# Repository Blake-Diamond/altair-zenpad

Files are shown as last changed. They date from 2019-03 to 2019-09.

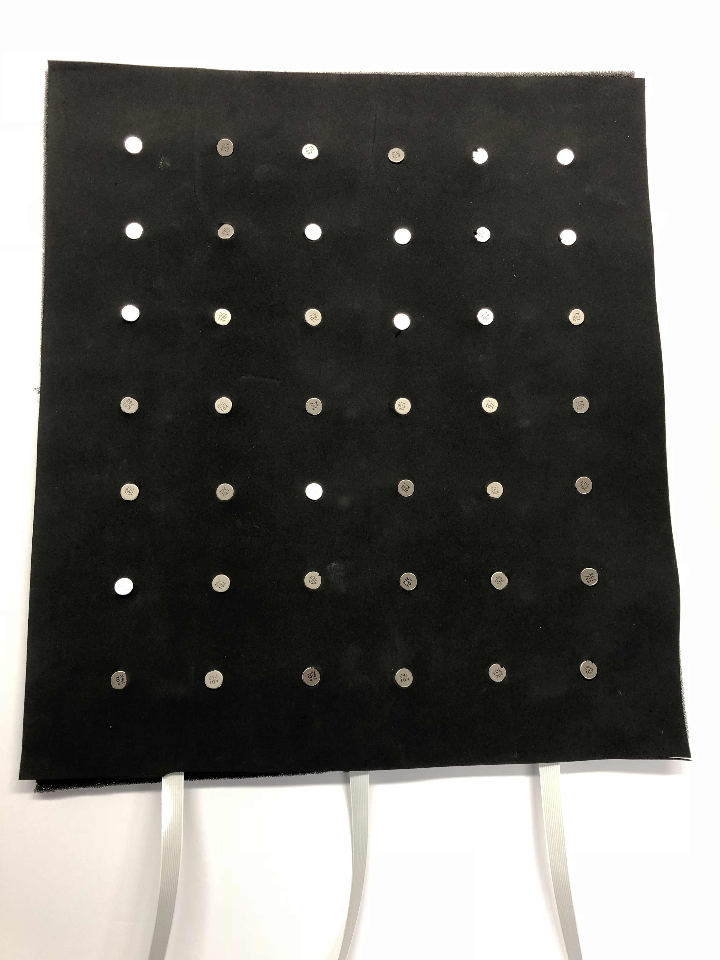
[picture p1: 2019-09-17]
Media/PHOTOS/image_67164417.JPG

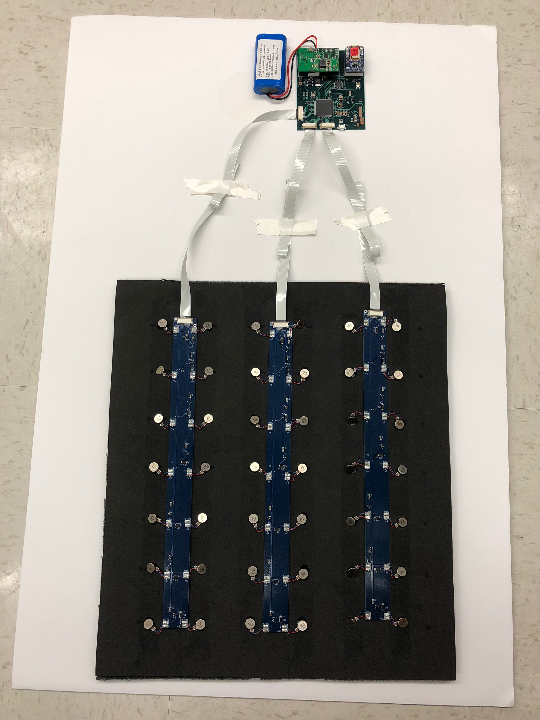
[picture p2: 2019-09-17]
Media/PHOTOS/IMG-0710.JPG

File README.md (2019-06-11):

# UC Santa Barbara - ECE Department 
## EE Capstone 2018-2019

### Contributors: Evan Blasband, Blake Diamond, Adam Gulliver, Zack Klebanoff

https://capstone.engineering.ucsb.edu/projects/altair-zenpad

This repository contains all of our arduino and android studio code for Altair Zenpad, a smart massage pad that you can control from your fingertips. There are 3 imporant aspect of this respository that contiain all of the necessary reference documents for future development and use of the ZenPad, described below:

## Hardware

PCB/Altair Massage Pad: contains all PCB projects (EAGLE) for Main and Peripheral PCB.

## Firmware

Winter_Demo: This folder contains all of the firmware that is need to flash the Teensy 3.6 using the Arduino IDE. This includes all associated header files that support use of the Bluetooth and PMIC. Some small changes are needed in order to program a Teensy board with the Arduino IDE, which can be found here: https://www.pjrc.com/teensy/tutorial.html

## Software

Zenpad-App/ZenPad: This folder contains the software project for the ZenPad app, which can be accessed by downloading and opening with Android Studio. Someone with Android SW development experience is needed in order to properly open and run the app, which was developed on a Nexus 5 phone.

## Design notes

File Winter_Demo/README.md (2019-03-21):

Code for Winter Demo

Combines operating the motors via simple bluetooth communication and incorporates simple reading of the PMIC registers.

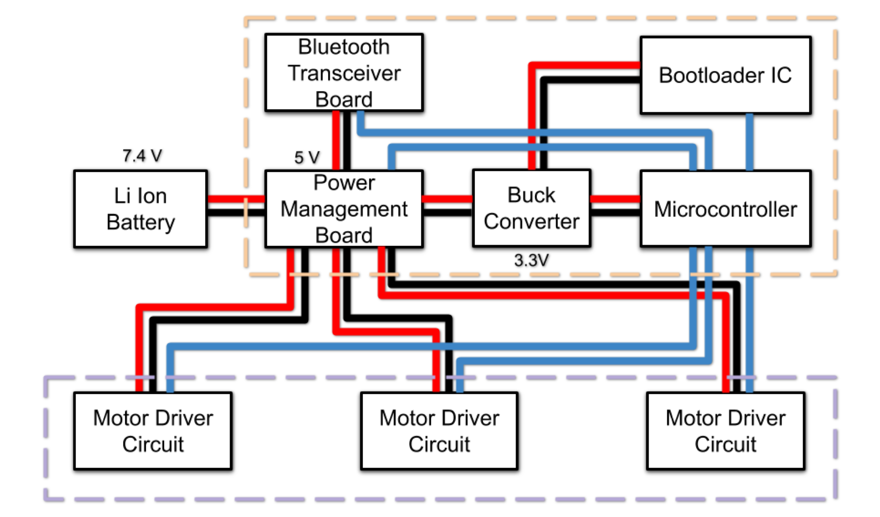
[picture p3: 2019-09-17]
Media/PHOTOS/Submitted images/blockDiagram.png

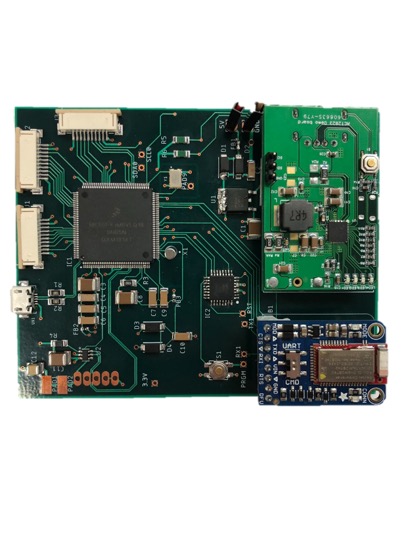
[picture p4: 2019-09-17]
Media/PHOTOS/Picture1.jpg

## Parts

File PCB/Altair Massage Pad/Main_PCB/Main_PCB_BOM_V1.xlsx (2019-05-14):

Part | Value | Device | Package | Description | ALLIED_NUMBER | ALLIED_PRICE-STOCK | DESCRIPTION | DIGI-KEY_PART_NUMBER | DIGI-KEY_PURCHASE_URL | HEIGHT | MANUFACTURER_NAME | MANUFACTURER_PART_NUMBER | MF | MOUSER_PART_NUMBER | MOUSER_PRICE-STOCK | MP | MPN | OC_FARNELL | OC_NEWARK | PACKAGE | RS_PART_NUMBER | RS_PRICE-STOCK | SPICEPREFIX | TP_SIGNAL_NAME | VENDOR
B1 |  | FE08-1 | FE08-1 | Headers & Wire Housings PCB RECPT 8P W/HOOKS TOP ENTRY |  |  |  |  |  |  | Molex | 22-02-2085 |  | 538-22-02-2085 | https://www.mouser.com/ProductDetail/Molex/22-02-2085
C1 | 2.2uF | C-USC1812K | C1812K | CAPACITOR, American symbol |  |  |  |  |  | 2.5mm | KEMET | C1812C225K1RACTU |  | 80-C1812C225K1R | https://www.mouser.com/ProductDetail/KEMET/C1812C225K1RACTU |  |  |  |  |  |  |  | C
C2 | 0.1uF | C-USC1808 | C1808 | CAPACITOR, American symbol |  |  |  |  |  | 0.9mm | KEMET | C1808C104KCRACTU (https://www.mouser.com/ProductDetail/KEMET/C1808C104KCRACTU?qs=sGAEpiMZZMs0AnBnWHyRQOl0HKfxQ2GIqnSeW6m289A%3D) |  | 80-C1808C104KCR | https://www.mouser.com/Passive-Components/Capacitors/Ceramic-Capacitors/MLCCs-Multilayer-Ceramic-Capacitors/Multilayer-Ceramic-Capacitors-MLCC-SMD-SMT/_/N-bkr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 |  |  |  |  |  |  |  | C
C3 | 2.2uF | C-USC1812K | C1812K | CAPACITOR, American symbol |  |  |  |  |  | 2.5mm | KEMET | C1812C225K1RACTU |  | 80-C1812C225K1R | https://www.mouser.com/ProductDetail/KEMET/C1812C225K1RACTU |  |  |  |  |  |  |  | C
C4 | 10nF | C-USC1808 | C1808 | CAPACITOR, American symbol |  |  |  |  |  | 1.4mm | KEMET | C1808C103KCRACTU |  | 80-C1808C103KCR | https://www.mouser.com/ProductDetail/KEMET/C1808C103KCRACTU |  |  |  |  |  |  |  | C
C5 | 10nF | C-USC1808 | C1808 | CAPACITOR, American symbol |  |  |  |  |  | 1.4mm | KEMET | C1808C103KCRACTU |  | 80-C1808C103KCR | https://www.mouser.com/ProductDetail/KEMET/C1808C103KCRACTU |  |  |  |  |  |  |  | C
C6 | 0.1uF | C-USC1808 | C1808 | CAPACITOR, American symbol |  |  |  |  |  | 0.9mm | KEMET | C1808C104KCRACTU (https://www.mouser.com/ProductDetail/KEMET/C1808C104KCRACTU?qs=sGAEpiMZZMs0AnBnWHyRQOl0HKfxQ2GIqnSeW6m289A%3D) |  | 80-C1808C104KCR | https://www.mouser.com/Passive-Components/Capacitors/Ceramic-Capacitors/MLCCs-Multilayer-Ceramic-Capacitors/Multilayer-Ceramic-Capacitors-MLCC-SMD-SMT/_/N-bkr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 |  |  |  |  |  |  |  | C
C7 | 0.1uF | C-USC1808 | C1808 | CAPACITOR, American symbol |  |  |  |  |  | 0.9mm | KEMET | C1808C104KCRACTU (https://www.mouser.com/ProductDetail/KEMET/C1808C104KCRACTU?qs=sGAEpiMZZMs0AnBnWHyRQOl0HKfxQ2GIqnSeW6m289A%3D) |  | 80-C1808C104KCR | https://www.mouser.com/Passive-Components/Capacitors/Ceramic-Capacitors/MLCCs-Multilayer-Ceramic-Capacitors/Multilayer-Ceramic-Capacitors-MLCC-SMD-SMT/_/N-bkr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 |  |  |  |  |  |  |  | C
C8 | 2.2uF | C-USC1812K | C1812K | CAPACITOR, American symbol |  |  |  |  |  | 2.5mm | KEMET | C1812C225K1RACTU |  | 80-C1812C225K1R | https://www.mouser.com/ProductDetail/KEMET/C1812C225K1RACTU |  |  |  |  |  |  |  | C
C9 | 0.1uF | C-USC1808 | C1808 | CAPACITOR, American symbol |  |  |  |  |  | 0.9mm | KEMET | C1808C104KCRACTU (https://www.mouser.com/ProductDetail/KEMET/C1808C104KCRACTU?qs=sGAEpiMZZMs0AnBnWHyRQOl0HKfxQ2GIqnSeW6m289A%3D) |  | 80-C1808C104KCR | https://www.mouser.com/Passive-Components/Capacitors/Ceramic-Capacitors/MLCCs-Multilayer-Ceramic-Capacitors/Multilayer-Ceramic-Capacitors-MLCC-SMD-SMT/_/N-bkr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 |  |  |  |  |  |  |  | C
C10 | 0.1uF | C-USC1808 | C1808 | CAPACITOR, American symbol |  |  |  |  |  | 0.9mm | KEMET | C1808C104KCRACTU (https://www.mouser.com/ProductDetail/KEMET/C1808C104KCRACTU?qs=sGAEpiMZZMs0AnBnWHyRQOl0HKfxQ2GIqnSeW6m289A%3D) |  | 80-C1808C104KCR | https://www.mouser.com/Passive-Components/Capacitors/Ceramic-Capacitors/MLCCs-Multilayer-Ceramic-Capacitors/Multilayer-Ceramic-Capacitors-MLCC-SMD-SMT/_/N-bkr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 |  |  |  |  |  |  |  | C
C11 | 2.2uF | C-USC1812K | C1812K | CAPACITOR, American symbol |  |  |  |  |  | 2.5mm | KEMET | C1812C225K1RACTU |  | 80-C1812C225K1R | https://www.mouser.com/ProductDetail/KEMET/C1812C225K1RACTU |  |  |  |  |  |  |  | C
C12 | 100uF | C-USC1210K | C1210K | CAPACITOR, American symbol |  |  |  |  |  | 2.5mm | KEMET | C1210C107M9PACTU |  | 80-C1210C107M9P | https://www.mouser.com/ProductDetail/KEMET/C1210C107M9PACTU?qs=sGAEpiMZZMs0AnBnWHyRQHfJxnYD9SALBQq9sfXwQCA%3D |  |  |  |  |  |  |  | C
D1 | MRA4004T3G | MRA4004T3G | DIOM5226X220N | Rectifier diode,MRA4004 1A 400V ON Semi MRA4004T3G, SMT Switching Diode, 400V 1A, 2-Pin DO-214AC | 70340468 | http://www.alliedelec.com/on-semiconductor-mra4004t3g/70340468/ | Rectifier diode,MRA4004 1A 400V ON Semi MRA4004T3G, SMT Switching Diode, 400V 1A, 2-Pin DO-214AC |  |  | 2.2mm | ON Semiconductor | MRA4004T3G |  | 863-MRA4004T3G | https://www.mouser.com/Search/Refine.aspx?Keyword=863-MRA4004T3G |  |  |  |  |  | 6490904 | http://uk.rs-online.com/web/p/products/6490904
D2 | MRA4004T3G | MRA4004T3G | DIOM5226X220N | Rectifier diode,MRA4004 1A 400V ON Semi MRA4004T3G, SMT Switching Diode, 400V 1A, 2-Pin DO-214AC | 70340468 | http://www.alliedelec.com/on-semiconductor-mra4004t3g/70340468/ | Rectifier diode,MRA4004 1A 400V ON Semi MRA4004T3G, SMT Switching Diode, 400V 1A, 2-Pin DO-214AC |  |  | 2.2mm | ON Semiconductor | MRA4004T3G |  | 863-MRA4004T3G | https://www.mouser.com/Search/Refine.aspx?Keyword=863-MRA4004T3G |  |  |  |  |  | 6490904 | http://uk.rs-online.com/web/p/products/6490904
D3 | MRA4004T3G | MRA4004T3G | DIOM5226X220N | Rectifier diode,MRA4004 1A 400V ON Semi MRA4004T3G, SMT Switching Diode, 400V 1A, 2-Pin DO-214AC | 70340468 | http://www.alliedelec.com/on-semiconductor-mra4004t3g/70340468/ | Rectifier diode,MRA4004 1A 400V ON Semi MRA4004T3G, SMT Switching Diode, 400V 1A, 2-Pin DO-214AC |  |  | 2.2mm | ON Semiconductor | MRA4004T3G |  | 863-MRA4004T3G | https://www.mouser.com/Search/Refine.aspx?Keyword=863-MRA4004T3G |  |  |  |  |  | 6490904 | http://uk.rs-online.com/web/p/products/6490904
D4 | MRA4004T3G | MRA4004T3G | DIOM5226X220N | Rectifier diode,MRA4004 1A 400V ON Semi MRA4004T3G, SMT Switching Diode, 400V 1A, 2-Pin DO-214AC | 70340468 | http://www.alliedelec.com/on-semiconductor-mra4004t3g/70340468/ | Rectifier diode,MRA4004 1A 400V ON Semi MRA4004T3G, SMT Switching Diode, 400V 1A, 2-Pin DO-214AC |  |  | 2.2mm | ON Semiconductor | MRA4004T3G |  | 863-MRA4004T3G | https://www.mouser.com/Search/Refine.aspx?Keyword=863-MRA4004T3G |  |  |  |  |  | 6490904 | http://uk.rs-online.com/web/p/products/6490904
FB1 | BLM15HB121SN1 | BLM15HB121SN1 | 402 | Ferrite Beads 0402 120ohms 500mA Auto Infotainment |  |  |  |  |  | .5mm | Murata | BLM15AG121SZ1D |  | 81-BLM15AG121SZ1D | https://www.mouser.com/ProductDetail/Murata-Electronics/BLM15AG121SZ1D?qs=lEfY3O89Aqn9v4OKM7sPMQ%3D%3D
FB2 | BLM15HB121SN1 | BLM15HB121SN1 | 402 | Ferrite Beads 0402 600ohms 25% General Signal Line |  |  |  |  |  | .5mm | TDK | MMZ1005S601HT000 |  | 810-MMZ1005S601HT000 | https://www.mouser.com/ProductDetail/TDK/MMZ1005S601HT000
FB3 | BLM15HB121SN1 | BLM15HB121SN1 | 402 | Ferrite Beads 0402 600ohms 25% General Signal Line |  |  |  |  |  | .5mm | TDK | MMZ1005S601HT000 |  | 810-MMZ1005S601HT000 | https://www.mouser.com/ProductDetail/TDK/MMZ1005S601HT000
IC1 | MK66FX1M0VLQ18 | MK66FX1M0VLQ18 | QFP50P2200X2200X160-144N | NXP - MK66FX1M0VLQ18 - MPU, ARM CORTEX-M4F, 180MHZ, LQFP-144 |  |  | NXP - MK66FX1M0VLQ18 - MPU, ARM CORTEX-M4F, 180MHZ, LQFP-144 |  |  | 1.6mm | Nexperia | MK66FX1M0VLQ18 |  | 841-MK66FX1M0VLQ18 | https://www.mouser.com/Search/Refine.aspx?Keyword=841-MK66FX1M0VLQ18
IC2 | MKL04Z32VLC4R | MKL04Z32VLC4R | QFP80P900X900X160-32N | ***WE WILL SEND THIS PART*** IC MCU 32BIT 32KB FLASH 32LQFP |  |  | IC MCU 32BIT 32KB FLASH 32LQFP |  |  | 1.6mm | Nexperia | MKL04Z32VLC4R |  | N/A | https://www.mouser.com/Search/Refine.aspx?Keyword=N%2FA
J1 | 52271-1079 | 52271-1079 | 52271-1079 | 1.0MM FPC R/A CONN 10 W Molex FFC/FPC SMT Series 1mm Pitch 10 Way Right Angle SMT Female FPC Connector, ZIF Bottom Contact | 70373119 | https://www.alliedelec.com/molex-incorporated-52271-1079/70373119/ | 1.0MM FPC R/A CONN 10 W Molex FFC/FPC SMT Series 1mm Pitch 10 Way Right Angle SMT Female FPC Connector, ZIF Bottom Contact |  |  |  | Molex | 52271-1079 |  | 538-52271-1079 | https://www.mouser.com/Search/Refine.aspx?Keyword=538-52271-1079 |  |  |  |  |  | 5144329P | http://uk.rs-online.com/web/p/products/5144329P
J2 | 52271-1079 | 52271-1079 | 52271-1079 | 1.0MM FPC R/A CONN 10 W Molex FFC/FPC SMT Series 1mm Pitch 10 Way Right Angle SMT Female FPC Connector, ZIF Bottom Contact | 70373119 | https://www.alliedelec.com/molex-incorporated-52271-1079/70373119/ | 1.0MM FPC R/A CONN 10 W Molex FFC/FPC SMT Series 1mm Pitch 10 Way Right Angle SMT Female FPC Connector, ZIF Bottom Contact |  |  |  | Molex | 52271-1079 |  | 538-52271-1079 | https://www.mouser.com/Search/Refine.aspx?Keyword=538-52271-1079 |  |  |  |  |  | 5144329P | http://uk.rs-online.com/web/p/products/5144329P
J3 | 52271-1079 | 52271-1079 | 52271-1079 | 1.0MM FPC R/A CONN 10 W Molex FFC/FPC SMT Series 1mm Pitch 10 Way Right Angle SMT Female FPC Connector, ZIF Bottom Contact | 70373119 | https://www.alliedelec.com/molex-incorporated-52271-1079/70373119/ | 1.0MM FPC R/A CONN 10 W Molex FFC/FPC SMT Series 1mm Pitch 10 Way Right Angle SMT Female FPC Connector, ZIF Bottom Contact |  |  |  | Molex | 52271-1079 |  | 538-52271-1079 | https://www.mouser.com/Search/Refine.aspx?Keyword=538-52271-1079 |  |  |  |  |  | 5144329P | http://uk.rs-online.com/web/p/products/5144329P
R1 | 33 | R-US_R1206 | R1206 | Thick Film Resistors - SMD 1K 1% |  |  |  |  |  | .6mm | Bourns | CR1206-FX-1001ELF |  | 652-CR1206FX-1001ELF | https://www.mouser.com/ProductDetail/Bourns/CR1206-FX-1001ELF
R2 | 33 | R-US_R1206 | R1206 | Thick Film Resistors - SMD 1K 1% |  |  |  |  |  | .6mm | Bourns | CR1206-FX-1001ELF |  | 652-CR1206FX-1001ELF | https://www.mouser.com/ProductDetail/Bourns/CR1206-FX-1001ELF
R3 | 470 | R-US_R1206 | R1206 | Thick Film Resistors - SMD CRGP 1206 470R 1% SMD Resistor |  |  |  |  |  | .55mm | TE Connectivity / Holsworthy | CRGP1206F470R |  | 279-CRGP1206F470R | https://www.mouser.com/ProductDetail/TE-Connectivity-Holsworthy/CRGP1206F470R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
R4 | 100k | R-US_R1206 | R1206 | Thick Film Resistors - SMD 0.5watt 100Kohms 1% 100ppm |  |  |  |  |  | 0.55mm | Vishay | RCS1206100KFKEA |  | 71-RCS1206100KFKEA | https://www.mouser.com/ProductDetail/Vishay-Dale/RCS1206100KFKEA
R5 | 4.7k | R-US_R1206 | R1206 | Thick Film Resistors - SMD 4.7K ohm 0.5% 0.5W AEC-Q200 |  |  |  |  |  | .6mm | KOA Speer | SG73G2BTTD4701D |  | 660-SG73G2BTTD4701D | https://www.mouser.com/ProductDetail/KOA-Speer/SG73G2BTTD4701D
R6 | 4.7k | R-US_R1206 | R1206 | Thick Film Resistors - SMD 4.7K ohm 0.5% 0.5W AEC-Q200 |  |  |  |  |  | .6mm | KOA Speer | SG73G2BTTD4701D |  | 660-SG73G2BTTD4701D | https://www.mouser.com/ProductDetail/KOA-Speer/SG73G2BTTD4701D
S1 |  | RS-187R05A2-DSMTRT | RS-187R05A2-DSMTRT | Tactile Switch SPST-NO Top Actuated Surface Mount, |  |  |  |  |  |  | C&K Switches | RS187R05A2DSMTRT |  | 611-RS187R05A2DSMTRT | https://www.mouser.com/ProductDetail/CK/RS187R05A2DSMTRT
SV2 |  | FE05-1 | FE05-1 | Headers & Wire Housings PCB RECPT 5P W/HOOKS TOP ENTRY |  |  |  |  |  |  | MOLEX | 38-00-1425 |  | 538-38-00-1425 | https://www.mouser.com/ProductDetail/Molex/38-00-1425 |  |  | unknown | unknown
U$1 | MICRO-USB | MICRO-USB | MICRO-USB | USB Connectors 5P RECEPTACLE |  |  |  |  |  |  | Hirose Connector | ZX62D-B-5PA8(30) |  | 798-ZX62D-B-5PA830 | https://www.mouser.com/ProductDetail/Hirose-Connector/ZX62D-B-5PA830
U1 | LP38691DT-3.3/NOPB | LP38691DT-3.3/NOPB | TD03B |  |  |  |  |  |  |  |  | LP38691DT3.3NOPB |  |  |  |  |  |  |  |  |  |  |  |  | Texas Instruments
U2 | TPD3S014DBVR | TPD3S014DBVR | DBV6 |  |  |  |  |  |  |  |  | TPD3S014DBVR |  |  |  |  |  |  |  |  |  |  |  |  | Texas Instruments
X1 | AB38T-32.768KHZ | AB38T-32.768KHZ | XTAL_AB38T-32.768KHZ | AB38T Series 32.768 kHz ¬±20 ppm 12.5 pF -10 to +60 ¬∞C Tuning Fork Crystal |  |  | AB38T Series 32.768 kHz ¬±20 ppm 12.5 pF -10 to +60 ¬∞C Tuning Fork Crystal | 535-9034-ND | https://www.digikey.com/product-detail/en/abracon-llc/AB38T-32.768KHZ/535-9034-ND/675229 |  |  |  | Abracon |  |  | AB38T-32.768KHZ |  |  |  | Cylindrical Can Radial Abracon
Y1 | ECS-160-8-30B-CKM | ECS-160-8-30B-CKM | XTAL_ECS-160-8-30B-CKM | The ECX-53B is a miniature SMD Crystal with a 3.2 x 5 mm |  |  | Crystal 16.0000mhz 8pf Smd | XC1839CT-ND | https://www.digikey.com/product-detail/en/ecs-inc/ECS-160-8-30B-CKM/XC1839CT-ND/2781964 |  |  |  | ECS Inc. |  |  | ECS-160-8-30B-CKM |  |  |  | SMD-4 ECS International

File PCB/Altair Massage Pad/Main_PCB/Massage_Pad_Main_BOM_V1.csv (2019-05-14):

Part | Value | Device | Package | Description | ALLIED_NUMBER | ALLIED_PRICE-STOCK | DESCRIPTION | DIGI-KEY_PART_NUMBER | DIGI-KEY_PURCHASE_URL | HEIGHT | MANUFACTURER_NAME | MANUFACTURER_PART_NUMBER | MF | MOUSER_PART_NUMBER | MOUSER_PRICE-STOCK | MP | MPN | OC_FARNELL | OC_NEWARK | PACKAGE | RS_PART_NUMBER | RS_PRICE-STOCK | SPICEPREFIX | TP_SIGNAL_NAME | VENDOR
3.3V |  | 1,6/0,8 | 1,6/0,8 | THROUGH-HOLE PAD
5V |  | 3,17/1,3 | 3,17/1,3 | THROUGH-HOLE PAD
B1 |  | BT-BLE-2479 | BT-BLE-2479 | Adafruit bluetooth BLE module for mounting onto PCB.
C1 | 2.2uF | C-USC1808 | C1808 | CAPACITOR, American symbol |  |  |  |  |  |  |  |  |  |  |  |  |  |  |  |  |  |  | C
C2 | 0.1uF | C-USC1808 | C1808 | CAPACITOR, American symbol |  |  |  |  |  |  |  |  |  |  |  |  |  |  |  |  |  |  | C
C3 | 2.2uF | C-USC1808 | C1808 | CAPACITOR, American symbol |  |  |  |  |  |  |  |  |  |  |  |  |  |  |  |  |  |  | C
C4 | 10nF | C-USC1808 | C1808 | CAPACITOR, American symbol |  |  |  |  |  |  |  |  |  |  |  |  |  |  |  |  |  |  | C
C5 | 10nF | C-USC1808 | C1808 | CAPACITOR, American symbol |  |  |  |  |  |  |  |  |  |  |  |  |  |  |  |  |  |  | C
C6 | 0.1uF | C-USC1808 | C1808 | CAPACITOR, American symbol |  |  |  |  |  |  |  |  |  |  |  |  |  |  |  |  |  |  | C
C7 | 0.1uF | C-USC1808 | C1808 | CAPACITOR, American symbol |  |  |  |  |  |  |  |  |  |  |  |  |  |  |  |  |  |  | C
C8 | 2.2uF | C-USC1808 | C1808 | CAPACITOR, American symbol |  |  |  |  |  |  |  |  |  |  |  |  |  |  |  |  |  |  | C
C9 | 0.1uF | C-USC1808 | C1808 | CAPACITOR, American symbol |  |  |  |  |  |  |  |  |  |  |  |  |  |  |  |  |  |  | C
C10 | 0.1uF | C-USC1808 | C1808 | CAPACITOR, American symbol |  |  |  |  |  |  |  |  |  |  |  |  |  |  |  |  |  |  | C
C11 | 2.2uF | C-USC1808 | C1808 | CAPACITOR, American symbol |  |  |  |  |  |  |  |  |  |  |  |  |  |  |  |  |  |  | C
C12 | 100uF | C-USC1808 | C1808 | CAPACITOR, American symbol |  |  |  |  |  |  |  |  |  |  |  |  |  |  |  |  |  |  | C
D1 | MRA4004T3G | MRA4004T3G | DIOM5226X220N | Rectifier diode,MRA4004 1A 400V ON Semi MRA4004T3G, SMT Switching Diode, 400V 1A, 2-Pin DO-214AC | 70340468 | http://www.alliedelec.com/on-semiconductor-mra4004t3g/70340468/ | Rectifier diode,MRA4004 1A 400V ON Semi MRA4004T3G, SMT Switching Diode, 400V 1A, 2-Pin DO-214AC |  |  | 2.2mm | ON Semiconductor | MRA4004T3G |  | 863-MRA4004T3G | https://www.mouser.com/Search/Refine.aspx?Keyword=863-MRA4004T3G |  |  |  |  |  | 6490904 | http://uk.rs-online.com/web/p/products/6490904
D2 | MRA4004T3G | MRA4004T3G | DIOM5226X220N | Rectifier diode,MRA4004 1A 400V ON Semi MRA4004T3G, SMT Switching Diode, 400V 1A, 2-Pin DO-214AC | 70340468 | http://www.alliedelec.com/on-semiconductor-mra4004t3g/70340468/ | Rectifier diode,MRA4004 1A 400V ON Semi MRA4004T3G, SMT Switching Diode, 400V 1A, 2-Pin DO-214AC |  |  | 2.2mm | ON Semiconductor | MRA4004T3G |  | 863-MRA4004T3G | https://www.mouser.com/Search/Refine.aspx?Keyword=863-MRA4004T3G |  |  |  |  |  | 6490904 | http://uk.rs-online.com/web/p/products/6490904
D3 | MRA4004T3G | MRA4004T3G | DIOM5226X220N | Rectifier diode,MRA4004 1A 400V ON Semi MRA4004T3G, SMT Switching Diode, 400V 1A, 2-Pin DO-214AC | 70340468 | http://www.alliedelec.com/on-semiconductor-mra4004t3g/70340468/ | Rectifier diode,MRA4004 1A 400V ON Semi MRA4004T3G, SMT Switching Diode, 400V 1A, 2-Pin DO-214AC |  |  | 2.2mm | ON Semiconductor | MRA4004T3G |  | 863-MRA4004T3G | https://www.mouser.com/Search/Refine.aspx?Keyword=863-MRA4004T3G |  |  |  |  |  | 6490904 | http://uk.rs-online.com/web/p/products/6490904
D4 | MRA4004T3G | MRA4004T3G | DIOM5226X220N | Rectifier diode,MRA4004 1A 400V ON Semi MRA4004T3G, SMT Switching Diode, 400V 1A, 2-Pin DO-214AC | 70340468 | http://www.alliedelec.com/on-semiconductor-mra4004t3g/70340468/ | Rectifier diode,MRA4004 1A 400V ON Semi MRA4004T3G, SMT Switching Diode, 400V 1A, 2-Pin DO-214AC |  |  | 2.2mm | ON Semiconductor | MRA4004T3G |  | 863-MRA4004T3G | https://www.mouser.com/Search/Refine.aspx?Keyword=863-MRA4004T3G |  |  |  |  |  | 6490904 | http://uk.rs-online.com/web/p/products/6490904
FB1 | BLM15HB121SN1 | BLM15HB121SN1 | 0402 | EMIFIL (R) Chip Ferrite Bead for GHz Noise
FB2 | BLM15HB121SN1 | BLM15HB121SN1 | 0402 | EMIFIL (R) Chip Ferrite Bead for GHz Noise
FB3 | BLM15HB121SN1 | BLM15HB121SN1 | 0402 | EMIFIL (R) Chip Ferrite Bead for GHz Noise
GND |  | 3,17/1,3 | 3,17/1,3 | THROUGH-HOLE PAD
IC1 | MK66FX1M0VLQ18 | MK66FX1M0VLQ18 | QFP50P2200X2200X160-144N | NXP - MK66FX1M0VLQ18 - MPU, ARM CORTEX-M4F, 180MHZ, LQFP-144 |  |  | NXP - MK66FX1M0VLQ18 - MPU, ARM CORTEX-M4F, 180MHZ, LQFP-144 |  |  | 1.6mm | Nexperia | MK66FX1M0VLQ18 |  | 841-MK66FX1M0VLQ18 | https://www.mouser.com/Search/Refine.aspx?Keyword=841-MK66FX1M0VLQ18
IC2 | MKL04Z32VLC4R | MKL04Z32VLC4R | QFP80P900X900X160-32N | IC MCU 32BIT 32KB FLASH 32LQFP |  |  | IC MCU 32BIT 32KB FLASH 32LQFP |  |  | 1.6mm | Nexperia | MKL04Z32VLC4R |  | N/A | https://www.mouser.com/Search/Refine.aspx?Keyword=N%2FA
J1 | 52271-1079 | 52271-1079 | 52271-1079 | 1.0MM FPC R/A CONN 10 W Molex FFC/FPC SMT Series 1mm Pitch 10 Way Right Angle SMT Female FPC Connector, ZIF Bottom Contact | 70373119 | https://www.alliedelec.com/molex-incorporated-52271-1079/70373119/ | 1.0MM FPC R/A CONN 10 W Molex FFC/FPC SMT Series 1mm Pitch 10 Way Right Angle SMT Female FPC Connector, ZIF Bottom Contact |  |  | mm | Molex | 52271-1079 |  | 538-52271-1079 | https://www.mouser.com/Search/Refine.aspx?Keyword=538-52271-1079 |  |  |  |  |  | 5144329P | http://uk.rs-online.com/web/p/products/5144329P
J2 | 52271-1079 | 52271-1079 | 52271-1079 | 1.0MM FPC R/A CONN 10 W Molex FFC/FPC SMT Series 1mm Pitch 10 Way Right Angle SMT Female FPC Connector, ZIF Bottom Contact | 70373119 | https://www.alliedelec.com/molex-incorporated-52271-1079/70373119/ | 1.0MM FPC R/A CONN 10 W Molex FFC/FPC SMT Series 1mm Pitch 10 Way Right Angle SMT Female FPC Connector, ZIF Bottom Contact |  |  | mm | Molex | 52271-1079 |  | 538-52271-1079 | https://www.mouser.com/Search/Refine.aspx?Keyword=538-52271-1079 |  |  |  |  |  | 5144329P | http://uk.rs-online.com/web/p/products/5144329P
J3 | 52271-1079 | 52271-1079 | 52271-1079 | 1.0MM FPC R/A CONN 10 W Molex FFC/FPC SMT Series 1mm Pitch 10 Way Right Angle SMT Female FPC Connector, ZIF Bottom Contact | 70373119 | https://www.alliedelec.com/molex-incorporated-52271-1079/70373119/ | 1.0MM FPC R/A CONN 10 W Molex FFC/FPC SMT Series 1mm Pitch 10 Way Right Angle SMT Female FPC Connector, ZIF Bottom Contact |  |  | mm | Molex | 52271-1079 |  | 538-52271-1079 | https://www.mouser.com/Search/Refine.aspx?Keyword=538-52271-1079 |  |  |  |  |  | 5144329P | http://uk.rs-online.com/web/p/products/5144329P
PAD1 |  | SMD5 | SMD2,54-5,08 | SMD PAD
PAD2 |  | SMD5 | SMD2,54-5,08 | SMD PAD
PAD9 |  | 1,6/0,8 | 1,6/0,8 | THROUGH-HOLE PAD
PRGM |  | 1,6/0,8 | 1,6/0,8 | THROUGH-HOLE PAD
R1 | 33 | R-EU_MELF0207W | MINI_MELF-0207W | RESISTOR, European symbol
R2 | 33 | R-EU_MELF0207W | MINI_MELF-0207W | RESISTOR, European symbol
R3 | 470 | R-EU_MELF0207W | MINI_MELF-0207W | RESISTOR, European symbol
R4 | 100k | R-EU_MELF0207W | MINI_MELF-0207W | RESISTOR, European symbol
R5 | 4.7k | R-EU_MELF0207W | MINI_MELF-0207W | RESISTOR, European symbol
R6 | 4.7k | R-EU_MELF0207W | MINI_MELF-0207W | RESISTOR, European symbol
RESET |  | 1,6/0,8 | 1,6/0,8 | THROUGH-HOLE PAD
RX1 |  | 1,6/0,8 | 1,6/0,8 | THROUGH-HOLE PAD
S1 |  | RS-187R05A2-DSMTRT | RS-187R05A2-DSMTRT | Tactile Switch SPST-NO Top Actuated Surface Mount,
SCL0 |  | 1,6/0,8 | 1,6/0,8 | THROUGH-HOLE PAD
SDA0 |  | 1,6/0,8 | 1,6/0,8 | THROUGH-HOLE PAD
SV2 |  | FE05-1 | FE05-1 | FEMALE HEADER |  |  |  |  |  |  |  |  |  |  |  |  |  | unknown | unknown
TP1 | TP5P5-25-13 | TP5P5-25-13 | P5-25-13 | Test pad
TX1 |  | 1,6/0,8 | 1,6/0,8 | THROUGH-HOLE PAD
U$1 | MICRO-USB | MICRO-USB | MICRO-USB | Micro USB B connector
U1 | LP38691DT-3.3/NOPB | LP38691DT-3.3/NOPB | TD03B |  |  |  |  |  |  |  |  | LP38691DT3.3NOPB |  |  |  |  |  |  |  |  |  |  |  |  | Texas Instruments
U2 | TPD3S014DBVR | TPD3S014DBVR | DBV6 |  |  |  |  |  |  |  |  | TPD3S014DBVR |  |  |  |  |  |  |  |  |  |  |  |  | Texas Instruments
X1 | AB38T-32.768KHZ | AB38T-32.768KHZ | XTAL_AB38T-32.768KHZ | AB38T Series 32.768 kHz ±20 ppm 12.5 pF -10 to +60 °C Tuning Fork Crystal |  |  | AB38T Series 32.768 kHz ±20 ppm 12.5 pF -10 to +60 °C Tuning Fork Crystal | 535-9034-ND | https://www.digikey.com/product-detail/en/abracon-llc/AB38T-32.768KHZ/535-9034-ND/675229 |  |  |  | Abracon |  |  | AB38T-32.768KHZ |  |  |  | Cylindrical Can Radial Abracon
Y1 | ECS-160-8-30B-CKM | ECS-160-8-30B-CKM | XTAL_ECS-160-8-30B-CKM | The ECX-53B is a miniature SMD Crystal with a 3.2 x 5 mm |  |  | Crystal 16.0000mhz 8pf Smd | XC1839CT-ND | https://www.digikey.com/product-detail/en/ecs-inc/ECS-160-8-30B-CKM/XC1839CT-ND/2781964 |  |  |  | ECS Inc. |  |  | ECS-160-8-30B-CKM |  |  |  | SMD-4 ECS International

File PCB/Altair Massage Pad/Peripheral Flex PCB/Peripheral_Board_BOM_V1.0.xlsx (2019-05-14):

Part | Value | Device | Package | Description | ALLIED_NUMBER | ALLIED_PRICE-STOCK | DESCRIPTION | HEIGHT | MANUFACTURER_NAME | MANUFACTURER_PART_NUMBER | MOUSER_PART_NUMBER | MOUSER_PRICE-STOCK | RS_PART_NUMBER | RS_PRICE-STOCK | SPICEPREFIX
5V |  | 3,17/1,3 | 3,17/1,3 | THROUGH-HOLE PAD
C1 | 0.1 uF | C-USC1808 | C1808 | CAPACITOR, American symbol |  |  |  |  | Kemet | C1808C104K5RACTU | 80-C1808C104K5R
C2 | 0.1 uF | C-USC1808 | C1808 | CAPACITOR, American symbol |  |  |  |  | Kemet | C1808C104K5RACTU | 80-C1808C104K5R
C3 | 0.1 uF | C-USC1808 | C1808 | CAPACITOR, American symbol |  |  |  |  | Kemet | C1808C104K5RACTU | 80-C1808C104K5R
C4 | 0.1 uF | C-USC1808 | C1808 | CAPACITOR, American symbol |  |  |  |  | Kemet | C1808C104K5RACTU | 80-C1808C104K5R
C5 | 0.1 uF | C-USC1808 | C1808 | CAPACITOR, American symbol |  |  |  |  | Kemet | C1808C104K5RACTU | 80-C1808C104K5R |  |  |  | C
C6 | 0.1 uF | C-USC1808 | C1808 | CAPACITOR, American symbol |  |  |  |  | Kemet | C1808C104K5RACTU | 80-C1808C104K5R
C7 | 0.1 uF | C-USC1808 | C1808 | CAPACITOR, American symbol |  |  |  |  | Kemet | C1808C104K5RACTU | 80-C1808C104K5R |  |  |  | C
D1 | MRA4004T3G | MRA4004T3G | DIOM5226X220N | Rectifier diode,MRA4004 1A 400V ON Semi MRA4004T3G, SMT Switching Diode, 400V 1A, 2-Pin DO-214AC | 70340468 | http://www.alliedelec.com/on-semiconductor-mra4004t3g/70340468/ | Rectifier diode,MRA4004 1A 400V ON Semi MRA4004T3G, SMT Switching Diode, 400V 1A, 2-Pin DO-214AC | 2.2mm | ON Semiconductor | MRA4004T3G | 863-MRA4004T3G | https://www.mouser.com/Search/Refine.aspx?Keyword=863-MRA4004T3G | 6490904 | http://uk.rs-online.com/web/p/products/6490904
D2 | MRA4004T3G | MRA4004T3G | DIOM5226X220N | Rectifier diode,MRA4004 1A 400V ON Semi MRA4004T3G, SMT Switching Diode, 400V 1A, 2-Pin DO-214AC | 70340468 | http://www.alliedelec.com/on-semiconductor-mra4004t3g/70340468/ | Rectifier diode,MRA4004 1A 400V ON Semi MRA4004T3G, SMT Switching Diode, 400V 1A, 2-Pin DO-214AC | 2.2mm | ON Semiconductor | MRA4004T3G | 863-MRA4004T3G | https://www.mouser.com/Search/Refine.aspx?Keyword=863-MRA4004T3G | 6490904 | http://uk.rs-online.com/web/p/products/6490904
D3 | MRA4004T3G | MRA4004T3G | DIOM5226X220N | Rectifier diode,MRA4004 1A 400V ON Semi MRA4004T3G, SMT Switching Diode, 400V 1A, 2-Pin DO-214AC | 70340468 | http://www.alliedelec.com/on-semiconductor-mra4004t3g/70340468/ | Rectifier diode,MRA4004 1A 400V ON Semi MRA4004T3G, SMT Switching Diode, 400V 1A, 2-Pin DO-214AC | 2.2mm | ON Semiconductor | MRA4004T3G | 863-MRA4004T3G | https://www.mouser.com/Search/Refine.aspx?Keyword=863-MRA4004T3G | 6490904 | http://uk.rs-online.com/web/p/products/6490904
D4 | MRA4004T3G | MRA4004T3G | DIOM5226X220N | Rectifier diode,MRA4004 1A 400V ON Semi MRA4004T3G, SMT Switching Diode, 400V 1A, 2-Pin DO-214AC | 70340468 | http://www.alliedelec.com/on-semiconductor-mra4004t3g/70340468/ | Rectifier diode,MRA4004 1A 400V ON Semi MRA4004T3G, SMT Switching Diode, 400V 1A, 2-Pin DO-214AC | 2.2mm | ON Semiconductor | MRA4004T3G | 863-MRA4004T3G | https://www.mouser.com/Search/Refine.aspx?Keyword=863-MRA4004T3G | 6490904 | http://uk.rs-online.com/web/p/products/6490904
D5 | MRA4004T3G | MRA4004T3G | DIOM5226X220N | Rectifier diode,MRA4004 1A 400V ON Semi MRA4004T3G, SMT Switching Diode, 400V 1A, 2-Pin DO-214AC | 70340468 | http://www.alliedelec.com/on-semiconductor-mra4004t3g/70340468/ | Rectifier diode,MRA4004 1A 400V ON Semi MRA4004T3G, SMT Switching Diode, 400V 1A, 2-Pin DO-214AC | 2.2mm | ON Semiconductor | MRA4004T3G | 863-MRA4004T3G | https://www.mouser.com/Search/Refine.aspx?Keyword=863-MRA4004T3G | 6490904 | http://uk.rs-online.com/web/p/products/6490904
D6 | MRA4004T3G | MRA4004T3G | DIOM5226X220N | Rectifier diode,MRA4004 1A 400V ON Semi MRA4004T3G, SMT Switching Diode, 400V 1A, 2-Pin DO-214AC | 70340468 | http://www.alliedelec.com/on-semiconductor-mra4004t3g/70340468/ | Rectifier diode,MRA4004 1A 400V ON Semi MRA4004T3G, SMT Switching Diode, 400V 1A, 2-Pin DO-214AC | 2.2mm | ON Semiconductor | MRA4004T3G | 863-MRA4004T3G | https://www.mouser.com/Search/Refine.aspx?Keyword=863-MRA4004T3G | 6490904 | http://uk.rs-online.com/web/p/products/6490904
D7 | MRA4004T3G | MRA4004T3G | DIOM5226X220N | Rectifier diode,MRA4004 1A 400V ON Semi MRA4004T3G, SMT Switching Diode, 400V 1A, 2-Pin DO-214AC | 70340468 | http://www.alliedelec.com/on-semiconductor-mra4004t3g/70340468/ | Rectifier diode,MRA4004 1A 400V ON Semi MRA4004T3G, SMT Switching Diode, 400V 1A, 2-Pin DO-214AC | 2.2mm | ON Semiconductor | MRA4004T3G | 863-MRA4004T3G | https://www.mouser.com/Search/Refine.aspx?Keyword=863-MRA4004T3G | 6490904 | http://uk.rs-online.com/web/p/products/6490904
GND |  | 3,17/1,3 | 3,17/1,3 | THROUGH-HOLE PAD
J1 | 52271-1079 | 52271-1079 | 52271-1079 | 1.0MM FPC R/A CONN 10 W Molex FFC/FPC SMT Series 1mm Pitch 10 Way Right Angle SMT Female FPC Connector, ZIF Bottom Contact | 70373119 | https://www.alliedelec.com/molex-incorporated-52271-1079/70373119/ | 1.0MM FPC R/A CONN 10 W Molex FFC/FPC SMT Series 1mm Pitch 10 Way Right Angle SMT Female FPC Connector, ZIF Bottom Contact | mm | Molex | 52271-1079 | 538-52271-1079 | https://www.mouser.com/Search/Refine.aspx?Keyword=538-52271-1079 | 5144329P | http://uk.rs-online.com/web/p/products/5144329P
Q1 | NX7002AKVL | NX7002AKVL | SOT95P230X110-3N | Trans MOSFET N-CH 60V 0.19A 3-Pin TO-236AB |  |  | Trans MOSFET N-CH 60V 0.19A 3-Pin TO-236AB | 1.1mm | Nexperia | NX7002AKVL | 771-NX7002AKVL | https://www.mouser.com/Search/Refine.aspx?Keyword=771-NX7002AKVL
Q2 | NX7002AKVL | NX7002AKVL | SOT95P230X110-3N | Trans MOSFET N-CH 60V 0.19A 3-Pin TO-236AB |  |  | Trans MOSFET N-CH 60V 0.19A 3-Pin TO-236AB | 1.1mm | Nexperia | NX7002AKVL | 771-NX7002AKVL | https://www.mouser.com/Search/Refine.aspx?Keyword=771-NX7002AKVL
Q3 | NX7002AKVL | NX7002AKVL | SOT95P230X110-3N | Trans MOSFET N-CH 60V 0.19A 3-Pin TO-236AB |  |  | Trans MOSFET N-CH 60V 0.19A 3-Pin TO-236AB | 1.1mm | Nexperia | NX7002AKVL | 771-NX7002AKVL | https://www.mouser.com/Search/Refine.aspx?Keyword=771-NX7002AKVL
Q4 | NX7002AKVL | NX7002AKVL | SOT95P230X110-3N | Trans MOSFET N-CH 60V 0.19A 3-Pin TO-236AB |  |  | Trans MOSFET N-CH 60V 0.19A 3-Pin TO-236AB | 1.1mm | Nexperia | NX7002AKVL | 771-NX7002AKVL | https://www.mouser.com/Search/Refine.aspx?Keyword=771-NX7002AKVL
Q5 | NX7002AKVL | NX7002AKVL | SOT95P230X110-3N | Trans MOSFET N-CH 60V 0.19A 3-Pin TO-236AB |  |  | Trans MOSFET N-CH 60V 0.19A 3-Pin TO-236AB | 1.1mm | Nexperia | NX7002AKVL | 771-NX7002AKVL | https://www.mouser.com/Search/Refine.aspx?Keyword=771-NX7002AKVL
Q6 | NX7002AKVL | NX7002AKVL | SOT95P230X110-3N | Trans MOSFET N-CH 60V 0.19A 3-Pin TO-236AB |  |  | Trans MOSFET N-CH 60V 0.19A 3-Pin TO-236AB | 1.1mm | Nexperia | NX7002AKVL | 771-NX7002AKVL | https://www.mouser.com/Search/Refine.aspx?Keyword=771-NX7002AKVL
Q7 | NX7002AKVL | NX7002AKVL | SOT95P230X110-3N | Trans MOSFET N-CH 60V 0.19A 3-Pin TO-236AB |  |  | Trans MOSFET N-CH 60V 0.19A 3-Pin TO-236AB | 1.1mm | Nexperia | NX7002AKVL | 771-NX7002AKVL | https://www.mouser.com/Search/Refine.aspx?Keyword=771-NX7002AKVL
R1 | 1k | R-US_R1206 | R1206 | RESISTOR, American symbol |  |  |  |  | Bourns | CR1206-FX-1001ELF | 652-CR1206FX-1001ELF |  |  |  | R
R2 | 1k | R-US_R1206 | R1206 | RESISTOR, American symbol |  |  |  |  | Bourns | CR1206-FX-1001ELF | 652-CR1206FX-1001ELF |  |  |  | R
R3 | 1k | R-US_R1206 | R1206 | RESISTOR, American symbol |  |  |  |  | Bourns | CR1206-FX-1001ELF | 652-CR1206FX-1001ELF |  |  |  | R
R4 | 1k | R-US_R1206 | R1206 | RESISTOR, American symbol |  |  |  |  | Bourns | CR1206-FX-1001ELF | 652-CR1206FX-1001ELF |  |  |  | R
R5 | 1k | R-US_R1206 | R1206 | RESISTOR, American symbol |  |  |  |  | Bourns | CR1206-FX-1001ELF | 652-CR1206FX-1001ELF |  |  |  | R
R6 | 1k | R-US_R1206 | R1206 | RESISTOR, American symbol |  |  |  |  | Bourns | CR1206-FX-1001ELF | 652-CR1206FX-1001ELF |  |  |  | R
R7 | 1k | R-US_R1206 | R1206 | RESISTOR, American symbol |  |  |  |  | Bourns | CR1206-FX-1001ELF | 652-CR1206FX-1001ELF |  |  |  | R

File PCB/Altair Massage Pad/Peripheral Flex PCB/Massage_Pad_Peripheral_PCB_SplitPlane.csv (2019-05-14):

Part | Value | Device | Package | Description | ALLIED_NUMBER | ALLIED_PRICE-STOCK | DESCRIPTION | HEIGHT | MANUFACTURER_NAME | MANUFACTURER_PART_NUMBER | MOUSER_PART_NUMBER | MOUSER_PRICE-STOCK | RS_PART_NUMBER | RS_PRICE-STOCK | SPICEPREFIX
5V |  | 3,17/1,3 | 3,17/1,3 | THROUGH-HOLE PAD
C1 | 0.1 uF | C-USC1808 | C1808 | CAPACITOR, American symbol |  |  |  |  | Kemet | C1808C104K5RACTU | 80-C1808C104K5R |  |  |  | C
C2 | 0.1 uF | C-USC1808 | C1808 | CAPACITOR, American symbol |  |  |  |  | Kemet | C1808C104K5RACTU | 80-C1808C104K5R |  |  |  | C
C3 | 0.1 uF | C-USC1808 | C1808 | CAPACITOR, American symbol |  |  |  |  | Kemet | C1808C104K5RACTU | 80-C1808C104K5R |  |  |  | C
C4 | 0.1 uF | C-USC1808 | C1808 | CAPACITOR, American symbol |  |  |  |  | Kemet | C1808C104K5RACTU | 80-C1808C104K5R |  |  |  | C
C5 | 0.1 uF | C-USC1808 | C1808 | CAPACITOR, American symbol |  |  |  |  | Kemet | C1808C104K5RACTU | 80-C1808C104K5R |  |  |  | C
C6 | 0.1 uF | C-USC1808 | C1808 | CAPACITOR, American symbol |  |  |  |  | Kemet | C1808C104K5RACTU | 80-C1808C104K5R |  |  |  | C
C7 | 0.1 uF | C-USC1808 | C1808 | CAPACITOR, American symbol |  |  |  |  | Kemet | C1808C104K5RACTU | 80-C1808C104K5R |  |  |  | C
D1 | MRA4004T3G | MRA4004T3G | DIOM5226X220N | Rectifier diode,MRA4004 1A 400V ON Semi MRA4004T3G, SMT Switching Diode, 400V 1A, 2-Pin DO-214AC | 70340468 | http://www.alliedelec.com/on-semiconductor-mra4004t3g/70340468/ | Rectifier diode,MRA4004 1A 400V ON Semi MRA4004T3G, SMT Switching Diode, 400V 1A, 2-Pin DO-214AC | 2.2mm | ON Semiconductor | MRA4004T3G | 863-MRA4004T3G | https://www.mouser.com/Search/Refine.aspx?Keyword=863-MRA4004T3G | 6490904 | http://uk.rs-online.com/web/p/products/6490904
D2 | MRA4004T3G | MRA4004T3G | DIOM5226X220N | Rectifier diode,MRA4004 1A 400V ON Semi MRA4004T3G, SMT Switching Diode, 400V 1A, 2-Pin DO-214AC | 70340468 | http://www.alliedelec.com/on-semiconductor-mra4004t3g/70340468/ | Rectifier diode,MRA4004 1A 400V ON Semi MRA4004T3G, SMT Switching Diode, 400V 1A, 2-Pin DO-214AC | 2.2mm | ON Semiconductor | MRA4004T3G | 863-MRA4004T3G | https://www.mouser.com/Search/Refine.aspx?Keyword=863-MRA4004T3G | 6490904 | http://uk.rs-online.com/web/p/products/6490904
D3 | MRA4004T3G | MRA4004T3G | DIOM5226X220N | Rectifier diode,MRA4004 1A 400V ON Semi MRA4004T3G, SMT Switching Diode, 400V 1A, 2-Pin DO-214AC | 70340468 | http://www.alliedelec.com/on-semiconductor-mra4004t3g/70340468/ | Rectifier diode,MRA4004 1A 400V ON Semi MRA4004T3G, SMT Switching Diode, 400V 1A, 2-Pin DO-214AC | 2.2mm | ON Semiconductor | MRA4004T3G | 863-MRA4004T3G | https://www.mouser.com/Search/Refine.aspx?Keyword=863-MRA4004T3G | 6490904 | http://uk.rs-online.com/web/p/products/6490904
D4 | MRA4004T3G | MRA4004T3G | DIOM5226X220N | Rectifier diode,MRA4004 1A 400V ON Semi MRA4004T3G, SMT Switching Diode, 400V 1A, 2-Pin DO-214AC | 70340468 | http://www.alliedelec.com/on-semiconductor-mra4004t3g/70340468/ | Rectifier diode,MRA4004 1A 400V ON Semi MRA4004T3G, SMT Switching Diode, 400V 1A, 2-Pin DO-214AC | 2.2mm | ON Semiconductor | MRA4004T3G | 863-MRA4004T3G | https://www.mouser.com/Search/Refine.aspx?Keyword=863-MRA4004T3G | 6490904 | http://uk.rs-online.com/web/p/products/6490904
D5 | MRA4004T3G | MRA4004T3G | DIOM5226X220N | Rectifier diode,MRA4004 1A 400V ON Semi MRA4004T3G, SMT Switching Diode, 400V 1A, 2-Pin DO-214AC | 70340468 | http://www.alliedelec.com/on-semiconductor-mra4004t3g/70340468/ | Rectifier diode,MRA4004 1A 400V ON Semi MRA4004T3G, SMT Switching Diode, 400V 1A, 2-Pin DO-214AC | 2.2mm | ON Semiconductor | MRA4004T3G | 863-MRA4004T3G | https://www.mouser.com/Search/Refine.aspx?Keyword=863-MRA4004T3G | 6490904 | http://uk.rs-online.com/web/p/products/6490904
D6 | MRA4004T3G | MRA4004T3G | DIOM5226X220N | Rectifier diode,MRA4004 1A 400V ON Semi MRA4004T3G, SMT Switching Diode, 400V 1A, 2-Pin DO-214AC | 70340468 | http://www.alliedelec.com/on-semiconductor-mra4004t3g/70340468/ | Rectifier diode,MRA4004 1A 400V ON Semi MRA4004T3G, SMT Switching Diode, 400V 1A, 2-Pin DO-214AC | 2.2mm | ON Semiconductor | MRA4004T3G | 863-MRA4004T3G | https://www.mouser.com/Search/Refine.aspx?Keyword=863-MRA4004T3G | 6490904 | http://uk.rs-online.com/web/p/products/6490904
D7 | MRA4004T3G | MRA4004T3G | DIOM5226X220N | Rectifier diode,MRA4004 1A 400V ON Semi MRA4004T3G, SMT Switching Diode, 400V 1A, 2-Pin DO-214AC | 70340468 | http://www.alliedelec.com/on-semiconductor-mra4004t3g/70340468/ | Rectifier diode,MRA4004 1A 400V ON Semi MRA4004T3G, SMT Switching Diode, 400V 1A, 2-Pin DO-214AC | 2.2mm | ON Semiconductor | MRA4004T3G | 863-MRA4004T3G | https://www.mouser.com/Search/Refine.aspx?Keyword=863-MRA4004T3G | 6490904 | http://uk.rs-online.com/web/p/products/6490904
GND |  | 3,17/1,3 | 3,17/1,3 | THROUGH-HOLE PAD
J1 | 52271-1079 | 52271-1079 | 52271-1079 | 1.0MM FPC R/A CONN 10 W Molex FFC/FPC SMT Series 1mm Pitch 10 Way Right Angle SMT Female FPC Connector, ZIF Bottom Contact | 70373119 | https://www.alliedelec.com/molex-incorporated-52271-1079/70373119/ | 1.0MM FPC R/A CONN 10 W Molex FFC/FPC SMT Series 1mm Pitch 10 Way Right Angle SMT Female FPC Connector, ZIF Bottom Contact | mm | Molex | 52271-1079 | 538-52271-1079 | https://www.mouser.com/Search/Refine.aspx?Keyword=538-52271-1079 | 5144329P | http://uk.rs-online.com/web/p/products/5144329P
PAD1 | MOT1+ | WIREPADSMD5-2,5 | 5-2,5 | Wire PAD connect wire on PCB
PAD2 | MOT1- | WIREPADSMD5-2,5 | 5-2,5 | Wire PAD connect wire on PCB
PAD3 | MOT2+ | WIREPADSMD5-2,5 | 5-2,5 | Wire PAD connect wire on PCB
PAD4 | MOT2- | WIREPADSMD5-2,5 | 5-2,5 | Wire PAD connect wire on PCB
PAD5 | MOT3+ | WIREPADSMD5-2,5 | 5-2,5 | Wire PAD connect wire on PCB
PAD6 | MOT3- | WIREPADSMD5-2,5 | 5-2,5 | Wire PAD connect wire on PCB
PAD7 | MOT4+ | WIREPADSMD5-2,5 | 5-2,5 | Wire PAD connect wire on PCB
PAD8 | MOT4- | WIREPADSMD5-2,5 | 5-2,5 | Wire PAD connect wire on PCB
PAD9 | MOT5+ | WIREPADSMD5-2,5 | 5-2,5 | Wire PAD connect wire on PCB
PAD10 | MOT5- | WIREPADSMD5-2,5 | 5-2,5 | Wire PAD connect wire on PCB
PAD11 | MOT6+ | WIREPADSMD5-2,5 | 5-2,5 | Wire PAD connect wire on PCB
PAD12 | MOT6- | WIREPADSMD5-2,5 | 5-2,5 | Wire PAD connect wire on PCB
PAD13 | MOT7+ | WIREPADSMD5-2,5 | 5-2,5 | Wire PAD connect wire on PCB
PAD14 | MOT7- | WIREPADSMD5-2,5 | 5-2,5 | Wire PAD connect wire on PCB
PAD15 | MOT1+ | WIREPADSMD5-2,5 | 5-2,5 | Wire PAD connect wire on PCB
PAD16 | MOT1- | WIREPADSMD5-2,5 | 5-2,5 | Wire PAD connect wire on PCB
PAD17 | MOT2+ | WIREPADSMD5-2,5 | 5-2,5 | Wire PAD connect wire on PCB
PAD18 | MOT2- | WIREPADSMD5-2,5 | 5-2,5 | Wire PAD connect wire on PCB
PAD19 | MOT3+ | WIREPADSMD5-2,5 | 5-2,5 | Wire PAD connect wire on PCB
PAD20 | MOT3- | WIREPADSMD5-2,5 | 5-2,5 | Wire PAD connect wire on PCB
PAD21 | MOT4+ | WIREPADSMD5-2,5 | 5-2,5 | Wire PAD connect wire on PCB
PAD22 | MOT4- | WIREPADSMD5-2,5 | 5-2,5 | Wire PAD connect wire on PCB
PAD23 | MOT5+ | WIREPADSMD5-2,5 | 5-2,5 | Wire PAD connect wire on PCB
PAD24 | MOT5- | WIREPADSMD5-2,5 | 5-2,5 | Wire PAD connect wire on PCB
PAD25 | MOT6+ | WIREPADSMD5-2,5 | 5-2,5 | Wire PAD connect wire on PCB
PAD26 | MOT6- | WIREPADSMD5-2,5 | 5-2,5 | Wire PAD connect wire on PCB
PAD27 | MOT7+ | WIREPADSMD5-2,5 | 5-2,5 | Wire PAD connect wire on PCB
PAD28 | MOT7- | WIREPADSMD5-2,5 | 5-2,5 | Wire PAD connect wire on PCB
Q1 | NX7002AKVL | NX7002AKVL | SOT95P230X110-3N | Trans MOSFET N-CH 60V 0.19A 3-Pin TO-236AB |  |  | Trans MOSFET N-CH 60V 0.19A 3-Pin TO-236AB | 1.1mm | Nexperia | NX7002AKVL | 771-NX7002AKVL | https://www.mouser.com/Search/Refine.aspx?Keyword=771-NX7002AKVL
Q2 | NX7002AKVL | NX7002AKVL | SOT95P230X110-3N | Trans MOSFET N-CH 60V 0.19A 3-Pin TO-236AB |  |  | Trans MOSFET N-CH 60V 0.19A 3-Pin TO-236AB | 1.1mm | Nexperia | NX7002AKVL | 771-NX7002AKVL | https://www.mouser.com/Search/Refine.aspx?Keyword=771-NX7002AKVL
Q3 | NX7002AKVL | NX7002AKVL | SOT95P230X110-3N | Trans MOSFET N-CH 60V 0.19A 3-Pin TO-236AB |  |  | Trans MOSFET N-CH 60V 0.19A 3-Pin TO-236AB | 1.1mm | Nexperia | NX7002AKVL | 771-NX7002AKVL | https://www.mouser.com/Search/Refine.aspx?Keyword=771-NX7002AKVL
Q4 | NX7002AKVL | NX7002AKVL | SOT95P230X110-3N | Trans MOSFET N-CH 60V 0.19A 3-Pin TO-236AB |  |  | Trans MOSFET N-CH 60V 0.19A 3-Pin TO-236AB | 1.1mm | Nexperia | NX7002AKVL | 771-NX7002AKVL | https://www.mouser.com/Search/Refine.aspx?Keyword=771-NX7002AKVL
Q5 | NX7002AKVL | NX7002AKVL | SOT95P230X110-3N | Trans MOSFET N-CH 60V 0.19A 3-Pin TO-236AB |  |  | Trans MOSFET N-CH 60V 0.19A 3-Pin TO-236AB | 1.1mm | Nexperia | NX7002AKVL | 771-NX7002AKVL | https://www.mouser.com/Search/Refine.aspx?Keyword=771-NX7002AKVL
Q6 | NX7002AKVL | NX7002AKVL | SOT95P230X110-3N | Trans MOSFET N-CH 60V 0.19A 3-Pin TO-236AB |  |  | Trans MOSFET N-CH 60V 0.19A 3-Pin TO-236AB | 1.1mm | Nexperia | NX7002AKVL | 771-NX7002AKVL | https://www.mouser.com/Search/Refine.aspx?Keyword=771-NX7002AKVL
Q7 | NX7002AKVL | NX7002AKVL | SOT95P230X110-3N | Trans MOSFET N-CH 60V 0.19A 3-Pin TO-236AB |  |  | Trans MOSFET N-CH 60V 0.19A 3-Pin TO-236AB | 1.1mm | Nexperia | NX7002AKVL | 771-NX7002AKVL | https://www.mouser.com/Search/Refine.aspx?Keyword=771-NX7002AKVL
R1 | 1k | R-US_R1206 | R1206 | RESISTOR, American symbol |  |  |  |  | Bourns | CR1206-FX-1001ELF | 652-CR1206FX-1001ELF |  |  |  | R
R2 | 1k | R-US_R1206 | R1206 | RESISTOR, American symbol |  |  |  |  |  |  |  |  |  |  | R
R3 | 1k | R-US_R1206 | R1206 | RESISTOR, American symbol |  |  |  |  |  |  |  |  |  |  | R
R4 | 1k | R-US_R1206 | R1206 | RESISTOR, American symbol |  |  |  |  |  |  |  |  |  |  | R
R5 | 1k | R-US_R1206 | R1206 | RESISTOR, American symbol |  |  |  |  |  |  |  |  |  |  | R
R6 | 1k | R-US_R1206 | R1206 | RESISTOR, American symbol |  |  |  |  |  |  |  |  |  |  | R
R7 | 1k | R-US_R1206 | R1206 | RESISTOR, American symbol |  |  |  |  |  |  |  |  |  |  | R

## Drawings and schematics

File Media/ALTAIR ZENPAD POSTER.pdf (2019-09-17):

# Evan Blasband | Blake Diamond | Adam Gulliver | Zackary Klebanoff

Background | Final Design

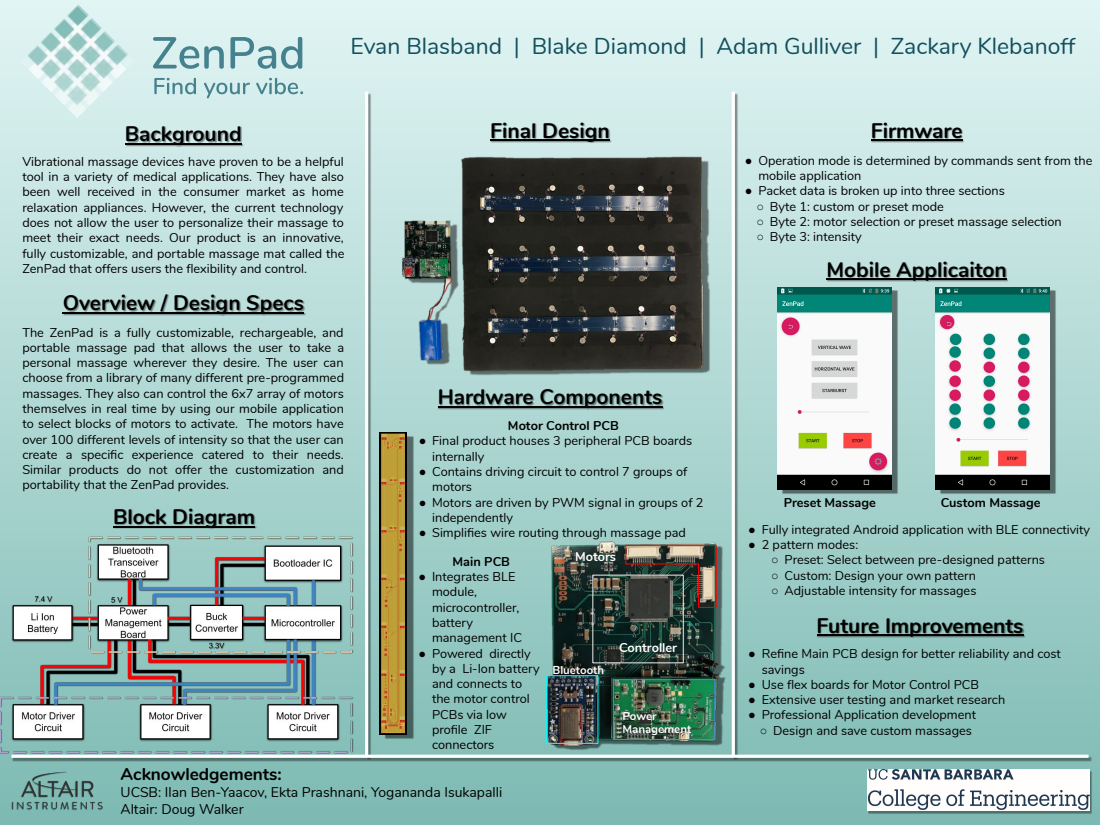
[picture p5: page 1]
Hardware Components; Block Diagram; Preset Massage; Custom Massage; Controller; Bluetooth; Motors; Power Management; Firmware

Vibrational massage devices have proven to be a helpful
tool in a variety of medical applications. They have also
been well received in the consumer market as home
relaxation appliances. However, the current technology
does not allow the user to personalize their massage to
meet their exact needs. Our product is an innovative,
fully customizable, and portable massage mat called the
ZenPad that offers users the flexibility and control.
Overview / Design Specs

● Operation mode is determined by commands sent from the
mobile application
● Packet data is broken up into three sections
○ Byte 1: custom or preset mode
○ Byte 2: motor selection or preset massage selection
○ Byte 3: intensity
Mobile Applicaiton

The ZenPad is a fully customizable, rechargeable, and
portable massage pad that allows the user to take a
personal massage wherever they desire. The user can
choose from a library of many different pre-programmed
massages. They also can control the 6x7 array of motors
themselves in real time by using our mobile application
to select blocks of motors to activate. The motors have
over 100 different levels of intensity so that the user can
create a specific experience catered to their needs.
Similar products do not offer the customization and
portability that the ZenPad provides.

Motor Control PCB

● Final product houses 3 peripheral PCB boards
internally
● Contains driving circuit to control 7 groups of
motors
● Motors are driven by PWM signal in groups of 2
independently
● Simplifies wire routing through massage pad
Main PCB
● Integrates BLE
module,
microcontroller,
battery
management IC
● Powered directly
by a Li-Ion battery
and connects to
the motor control
PCBs via low
profile ZIF
connectors

● Fully integrated Android application with BLE connectivity
● 2 pattern modes:
○ Preset: Select between pre-designed patterns
○ Custom: Design your own pattern
○ Adjustable intensity for massages
Future Improvements

● Refine Main PCB design for better reliability and cost
savings
● Use flex boards for Motor Control PCB
● Extensive user testing and market research
● Professional Application development
○ Design and save custom massages

Acknowledgements:
UCSB: Ilan Ben-Yaacov, Ekta Prashnani, Yogananda Isukapalli
Altair: Doug Walker

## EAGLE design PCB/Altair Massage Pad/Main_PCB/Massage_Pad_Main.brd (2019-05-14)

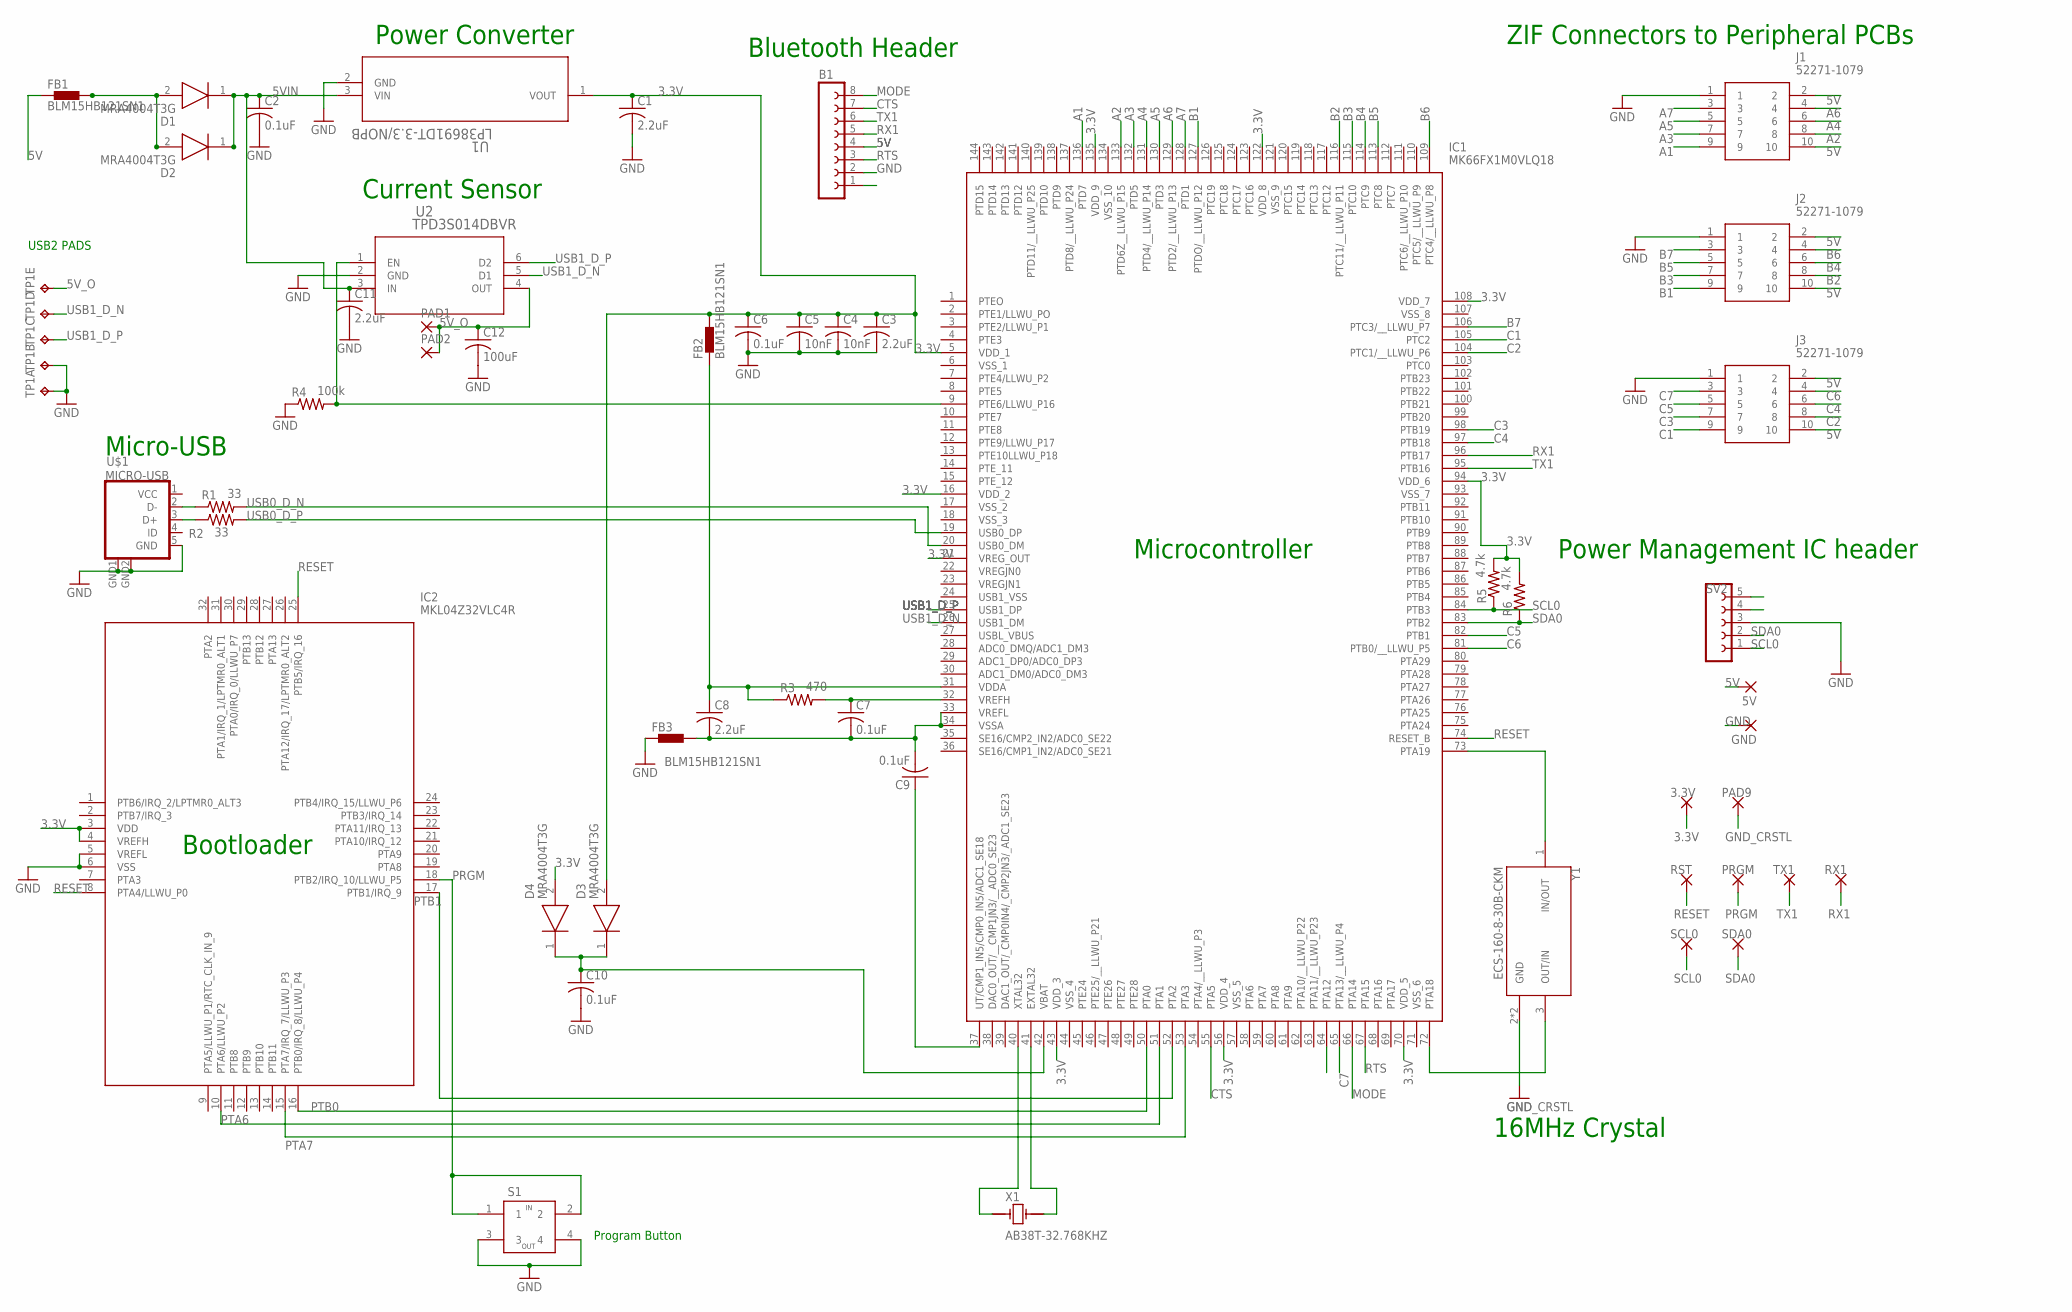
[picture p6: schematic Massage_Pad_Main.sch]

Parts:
3.3V: 1,6/0,8
5V: 3,17/1,3
B1: BT-BLE-2479
C1, C3, C8, C11: 2.2uF; C1812K
C2, C6, C7, C9, C10: 0.1uF; C1808
C4, C5: 10nF; C1808
C12: 100uF; C1210K
D1, D2, D3, D4: MRA4004T3G; DIOM5226X220N
FB1, FB2, FB3: BLM15HB121SN1; 0402
GND: 3,17/1,3
IC1: MK66FX1M0VLQ18; QFP50P2200X2200X160-144N
IC2: MKL04Z32VLC4R; QFP80P900X900X160-32N
J1, J2, J3: 52271-1079
PAD1, PAD2: SMD5; SMD2,54-5,08
PAD9: 1,6/0,8
PRGM: 1,6/0,8
R1, R2: 33; R1206
R3: 470; R1206
R4: 100k; R1206
R5, R6: 4.7k; R1206
RST: 1,6/0,8
RX1: 1,6/0,8
S1: RS-187R05A2-DSMTRT
SCL0: 1,6/0,8
SDA0: 1,6/0,8
SV2: FE05-1
TP1: TP5P5-25-13; P5-25-13
TX1: 1,6/0,8
U1: LP38691DT-3.3/NOPB; TD03B
U2: TPD3S014DBVR; DBV6
U$1: MICRO-USB
X1: AB38T-32.768KHZ; XTAL_AB38T-32.768KHZ
Y1: ECS-160-8-30B-CKM; XTAL_ECS-160-8-30B-CKM

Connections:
3.3V: 3.3V.1, C1.1, C3.1, C4.1, C5.1, C6.1, D3.2 (A), D4.2 (A), FB2.2, IC1.5 (VDD_1), IC1.16 (VDD_2), IC1.21 (VREG_OUT), IC1.43 (VDD_3), IC1.56 (VDD_4), IC1.70 (VDD_5), IC1.94 (VDD_6), IC1.108 (VDD_7), IC1.122 (VDD_8), IC1.135 (VDD_9), IC2.3 (VDD), IC2.4 (VREFH), R5.2, R6.2, U1.1 (VOUT)
5V: 5V.1, B1.4, FB1.1, J1.2, J1.10, J2.2, J2.10, J3.2, J3.10
5VIN: C2.1, C11.1, D1.1 (K), D2.1 (K), U1.3 (VIN), U2.3 (IN)
5V_O: C12.1, PAD1.1, PAD2.1, TP1.TP-5, U2.4 (OUT)
A1: IC1.136 (PTD7), J1.9
A2: IC1.133 (PTD6Z__LLWU_P15), J1.8
A3: IC1.132 (PTD5), J1.7
A4: IC1.131 (PTD4/__LLWU_P14), J1.6
A5: IC1.130 (PTD3), J1.5
A6: IC1.129 (PTD2/__LLWU_P13), J1.4
A7: IC1.128 (PTD1), J1.3
B1: IC1.127 (PTDO/__LLWU_P12), J2.9
B2: IC1.116 (PTC11/__LLWU_P11), J2.8
B3: IC1.115 (PTC10), J2.7
B4: IC1.114 (PTC9), J2.6
B5: IC1.113 (PTC8), J2.5
B6: IC1.109 (PTC4/__LLWU_P8), J2.4
B7: IC1.106 (PTC3/__LLWU_P7), J2.3
C1: IC1.105 (PTC2), J3.9
C2: IC1.104 (PTC1/__LLWU_P6), J3.8
C3: IC1.98 (PTB19), J3.7
C4: IC1.97 (PTB18), J3.6
C5: IC1.82 (PTB1), J3.5
C6: IC1.81 (PTB0/__LLWU_P5), J3.4
C7: IC1.65 (PTA13/__LLWU_P4), J3.3
CTS: B1.7, IC1.55 (PTA5)
DFU_5V: B1.1
GND: B1.2, C1.2, C2.2, C3.2, C4.2, C5.2, C6.2, C10.2, C11.2, C12.2, FB3.1, GND.1, IC2.5 (VREFL), IC2.6 (VSS), J1.1, J2.1, J3.1, R4.1, S1.3, S1.4, SV2.3, TP1.TP-1, TP1.TP-2, U1.2 (GND), U2.2 (GND), U$1.5 (GND), U$1.GND1 (GND), U$1.GND2 (GND)
GND_CRSTL: PAD9.1, Y1.2 (GND), Y1.4 (GND)
MODE: B1.8, IC1.66 (PTA14)
unnamed: C10.1, D3.1 (K), D4.1 (K), IC1.42 (VBAT)
unnamed: R1.1, U$1.2 (D-)
unnamed: R2.1, U$1.3 (D+)
unnamed: D1.2 (A), D2.2 (A), FB1.2
unnamed: IC1.73 (PTA19), Y1.1 (IN/OUT)
unnamed: C7.1, IC1.32 (VREFH), R3.2
unnamed: C7.2, C8.2, C9.2, FB3.2, IC1.33 (VREFL), IC1.34 (VSSA)
unnamed: C8.1, FB2.1, IC1.31 (VDDA), R3.1
unnamed: C9.1, IC1.37 (UT/CMP1_IN5/CMP0_IN5/ADC1_SE18)
unnamed: IC1.72 (PTA18), Y1.3 (OUT/IN)
unnamed: IC1.40 (XTAL32), X1.1
unnamed: IC1.41 (EXTAL32), X1.2
unnamed: IC1.9 (PTE6/LLWU_P16), R4.2, U2.1 (EN)
PRGM: IC2.18 (PTB2/IRQ_10/LLWU_P5), PRGM.1, S1.1, S1.2
PTA6: IC1.51 (PTA1), IC2.10 (PTA6/LLWU_P2)
PTA7: IC1.53 (PTA3), IC2.15 (PTA7/IRQ_7/LLWU_P3)
PTB0: IC1.50 (PTA0), IC2.16 (PTB0/IRQ_8/LLWU_P4)
PTB1: IC1.52 (PTA2), IC2.17 (PTB1/IRQ_9)
RESET: IC1.74 (RESET_B), IC2.8 (PTA4/LLWU_P0), IC2.25 (PTB5/IRQ_16), RST.1
RTS: B1.3, IC1.67 (PTA15)
RX1: B1.5, IC1.96 (PTB17), RX1.1
SCL0: IC1.84 (PTB3), R5.1, SCL0.1, SV2.1
SDA0: IC1.83 (PTB2), R6.1, SDA0.1, SV2.2
TX1: B1.6, IC1.95 (PTB16), TX1.1
USB0_D_N: IC1.20 (USB0_DM), R1.2
USB0_D_P: IC1.19 (USB0_DP), R2.2
USB1_D_N: IC1.26 (USB1_DM), TP1.TP-4, U2.5 (D1)
USB1_D_P: IC1.25 (USB1_DP), TP1.TP-3, U2.6 (D2)
VCC: U$1.1 (VCC)

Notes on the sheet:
Bluetooth Header
ZIF Connectors to Peripheral PCBs
Microcontroller
Bootloader
Micro-USB
Power Converter
Current Sensor
Power Management IC header
16MHz Crystal
Program Button
USB2 PADS

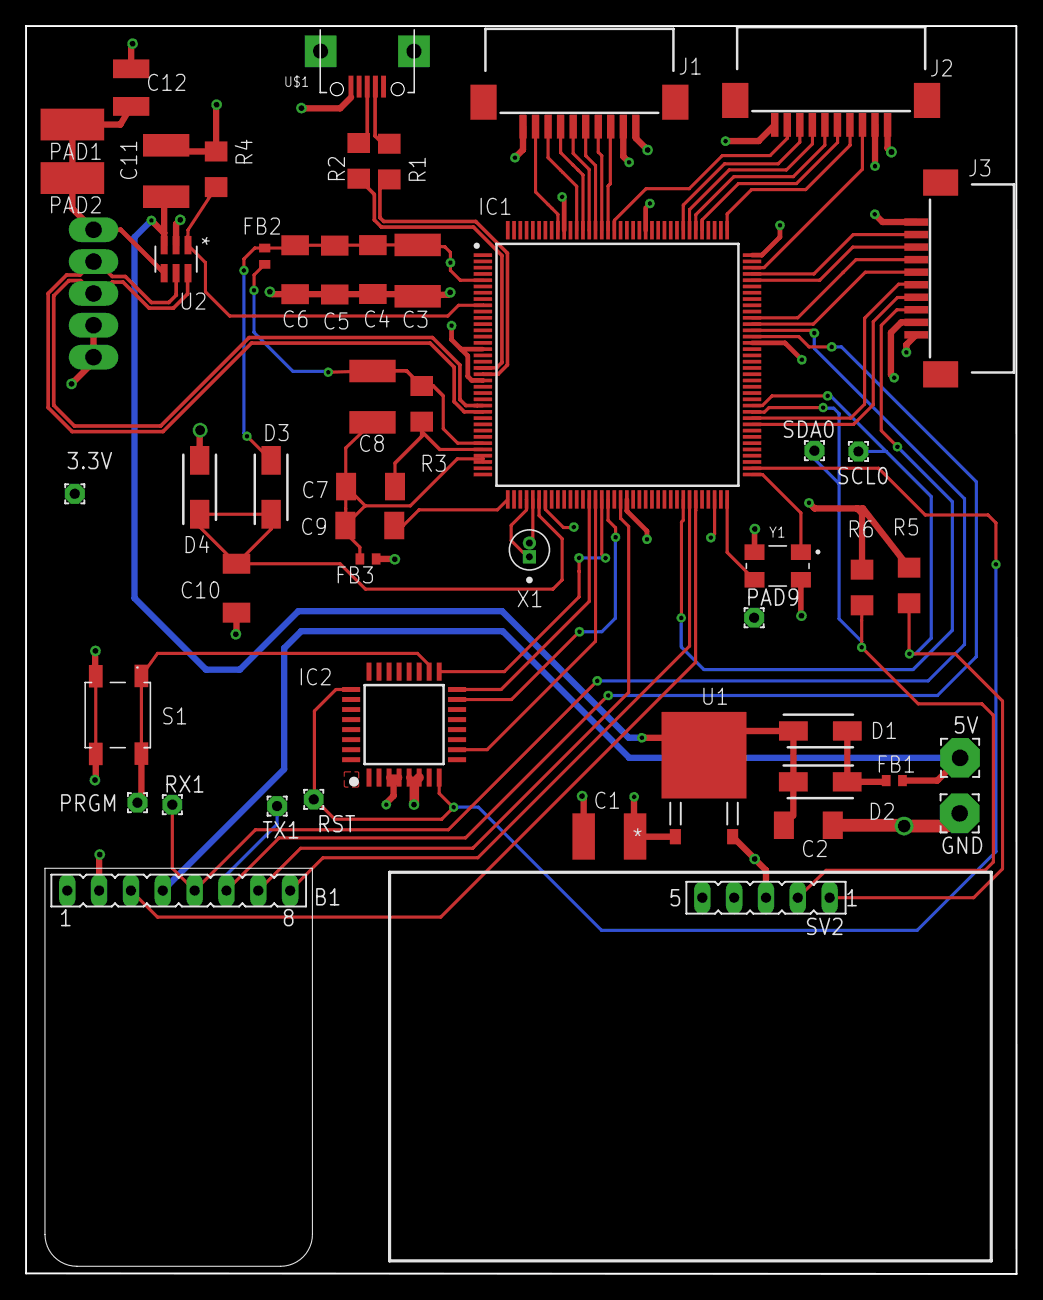
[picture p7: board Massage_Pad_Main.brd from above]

Board: 4 copper layers, 79.0 x 99.6 mm, 51 parts (0 on the bottom side), 57 nets.

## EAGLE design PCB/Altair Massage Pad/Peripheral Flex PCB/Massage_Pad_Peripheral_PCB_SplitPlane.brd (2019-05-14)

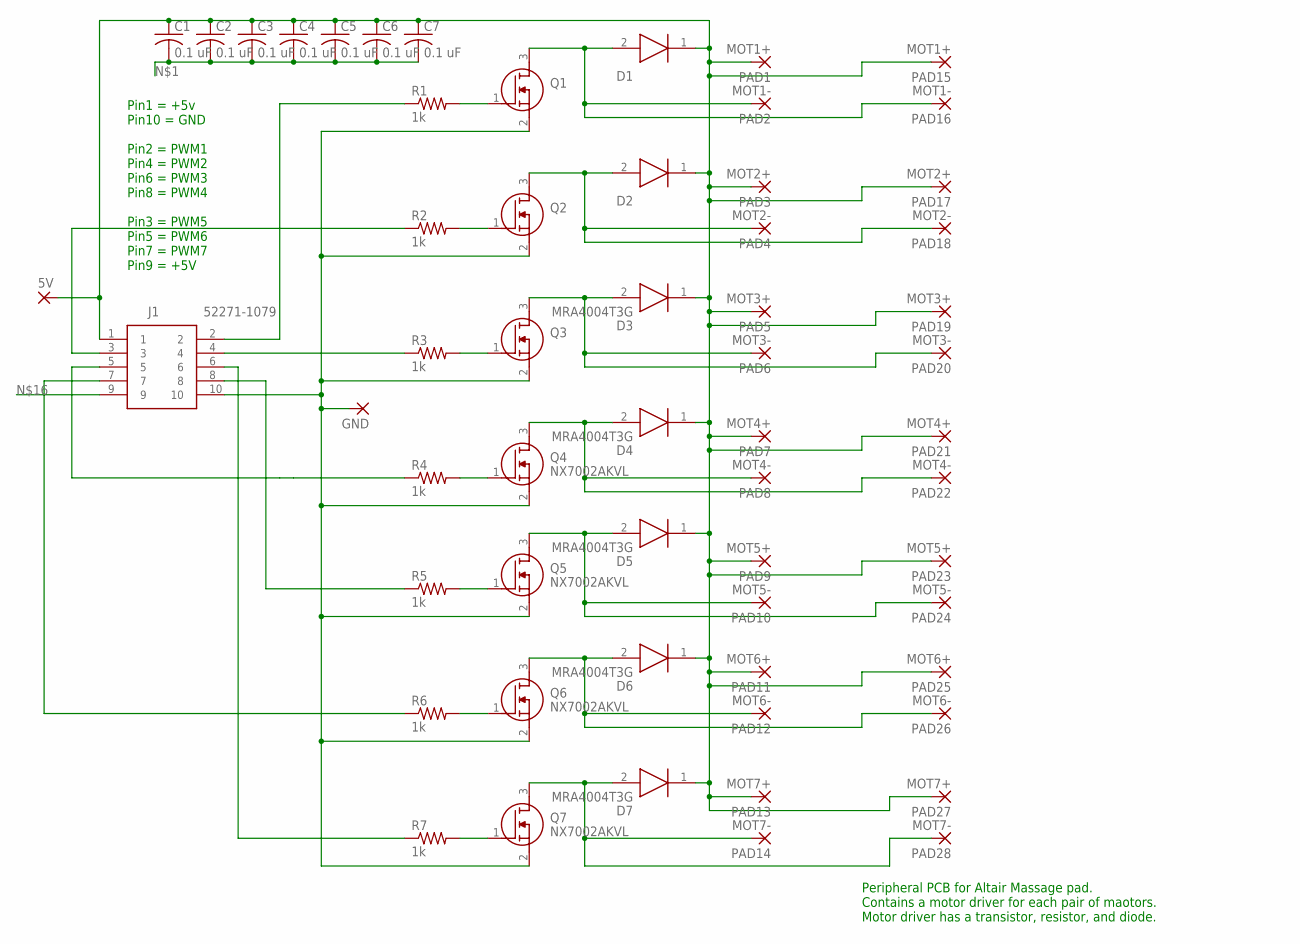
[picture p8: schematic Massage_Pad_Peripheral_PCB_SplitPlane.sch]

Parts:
5V: 3,17/1,3
C1, C2, C3, C4, C5, C6, C7: 0.1 uF; C1808; MANUFACTURER_PART_NUMBER C1808C104K5RACTU; MOUSER_PART_NUMBER 80-C1808C104K5R
D1, D2, D3, D4, D5, D6, D7: MRA4004T3G; DIOM5226X220N
GND: 3,17/1,3
J1: 52271-1079
PAD1, PAD15: MOT1+; 5-2,5
PAD2, PAD16: MOT1-; 5-2,5
PAD3, PAD17: MOT2+; 5-2,5
PAD4, PAD18: MOT2-; 5-2,5
PAD5, PAD19: MOT3+; 5-2,5
PAD6, PAD20: MOT3-; 5-2,5
PAD7, PAD21: MOT4+; 5-2,5
PAD8, PAD22: MOT4-; 5-2,5
PAD9, PAD23: MOT5+; 5-2,5
PAD10, PAD24: MOT5-; 5-2,5
PAD11, PAD25: MOT6+; 5-2,5
PAD12, PAD26: MOT6-; 5-2,5
PAD13, PAD27: MOT7+; 5-2,5
PAD14, PAD28: MOT7-; 5-2,5
Q1, Q2, Q3, Q4, Q5, Q6, Q7: NX7002AKVL; SOT95P230X110-3N
R1: 1k; R1206; MANUFACTURER_PART_NUMBER CR1206-FX-1001ELF; MOUSER_PART_NUMBER 652-CR1206FX-1001ELF
R2, R3, R4, R5, R6, R7: 1k; R1206

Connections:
unnamed: C1.2, C2.2, C3.2, C4.2, C5.2, C6.2, C7.2, GND.1, J1.10, Q1.2 (S), Q2.2 (S), Q3.2 (S), Q4.2 (S), Q5.2 (S), Q6.2 (S), Q7.2 (S)
unnamed: Q1.1 (G), R1.2
unnamed: Q2.1 (G), R2.2
unnamed: Q3.1 (G), R3.2
unnamed: Q4.1 (G), R4.2
unnamed: Q5.1 (G), R5.2
unnamed: Q6.1 (G), R6.2
unnamed: Q7.1 (G), R7.2
unnamed: D7.2 (A), PAD14.1, PAD28.1, Q7.3 (D)
unnamed: D6.2 (A), PAD12.1, PAD26.1, Q6.3 (D)
unnamed: D5.2 (A), PAD10.1, PAD24.1, Q5.3 (D)
unnamed: D3.2 (A), PAD6.1, PAD20.1, Q3.3 (D)
unnamed: D4.2 (A), PAD8.1, PAD22.1, Q4.3 (D)
unnamed: D2.2 (A), PAD4.1, PAD18.1, Q2.3 (D)
unnamed: D1.2 (A), PAD2.1, PAD16.1, Q1.3 (D)
unnamed: 5V.1, C1.1, C2.1, C3.1, C4.1, C5.1, C6.1, C7.1, D1.1 (K), D2.1 (K), D3.1 (K), D4.1 (K), D5.1 (K), D6.1 (K), D7.1 (K), J1.1, J1.9, PAD1.1, PAD3.1, PAD5.1, PAD7.1, PAD9.1, PAD11.1, PAD13.1, PAD15.1, PAD17.1, PAD19.1, PAD21.1, PAD23.1, PAD25.1, PAD27.1
unnamed: J1.2, R1.1
unnamed: J1.3, R2.1
unnamed: J1.4, R3.1
unnamed: J1.5, R4.1
unnamed: J1.8, R5.1
unnamed: J1.7, R6.1
unnamed: J1.6, R7.1

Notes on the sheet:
Peripheral PCB for Altair Massage pad. Contains a motor driver for each pair of maotors. Motor driver has a transistor, resistor, and diode.
Pin1 = +5v Pin10 = GND Pin2 = PWM1 Pin4 = PWM2 Pin6 = PWM3 Pin8 = PWM4 Pin3 = PWM5 Pin5 = PWM6 Pin7 = PWM7 Pin9 = +5V

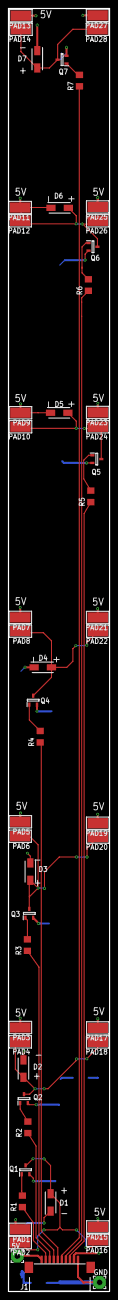
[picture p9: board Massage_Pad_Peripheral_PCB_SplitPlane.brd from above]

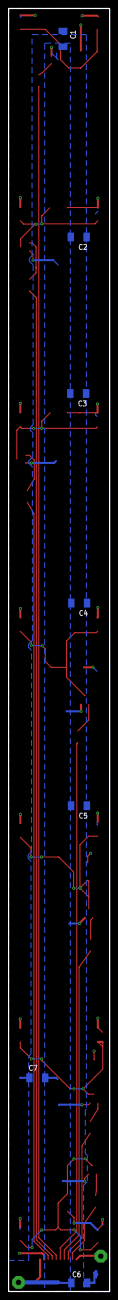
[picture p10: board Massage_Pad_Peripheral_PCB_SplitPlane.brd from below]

Board: 2 copper layers, 25.0 x 317.5 mm, 59 parts (7 on the bottom side), 23 nets.

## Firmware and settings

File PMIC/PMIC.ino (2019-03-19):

#include <Wire.h>

void setup() {
  // put your setup code here, to run once:
  
  Wire.begin();
  Serial.begin(9600);
  Wire.setSDA(18);
  Wire.setSCL(19);
  Wire.setClock(400000);

  delay(3000);

  SetDefault();

}

void loop() {

}

int ReadReg(int SlaveAddress, int Reg, int NumBytesRequest){
  byte RegRead;
  Wire.beginTransmission(SlaveAddress);
  Wire.write(Reg);
  Wire.requestFrom(SlaveAddress,NumBytesRequest);
  RegRead = Wire.read();
  Wire.endTransmission();
  Serial.println(RegRead);
}

int WriteReg(int SlaveAddress, int Reg, int WriteValue){
  Wire.beginTransmission(SlaveAddress);
  Wire.write(Reg);
  Wire.write(WriteValue);
  Wire.endTransmission();
}

int SetDefault(){
  WriteReg(90,1,0);
  WriteReg(90,2,0);
  WriteReg(90,3,136);
  WriteReg(90,4,153);
  WriteReg(90,5,146);
  WriteReg(90,6,0);
  WriteReg(90,7,0);
  WriteReg(90,8,0);
}

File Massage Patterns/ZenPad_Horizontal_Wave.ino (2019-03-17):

//Altair ZenPad Vertical Wave Prototype Script

const int L1 = 14;
const int C1 = 9;
const int R1 = 4;
const int L2 = 7;
const int C2 = 10;
const int R2 = 16;
const int L3 = 8;
const int C3 = 35;
const int R3 = 17;
const int L4 = 6;
const int C4 = 36;
const int R4 = 29;
const int L5 = 20;
const int C5 = 37;
const int R5 = 30;
const int L6 = 21;
const int C6 = 38;
const int R6 = 22;
const int L7 = 5;
const int C7 = 2;
const int R7 = 23;

void setup() {
  // put your setup code here, to run once:
  pinMode(L1, OUTPUT);
  pinMode(C1, OUTPUT);
  pinMode(R1, OUTPUT);
  pinMode(L2, OUTPUT);
  pinMode(C2, OUTPUT);
  pinMode(R2, OUTPUT);
  pinMode(L3, OUTPUT);
  pinMode(C3, OUTPUT);
  pinMode(R3, OUTPUT);
  pinMode(L4, OUTPUT);
  pinMode(C4, OUTPUT);
  pinMode(R4, OUTPUT);
  pinMode(L5, OUTPUT);
  pinMode(C5, OUTPUT);
  pinMode(R5, OUTPUT);
  pinMode(L6, OUTPUT);
  pinMode(C6, OUTPUT);
  pinMode(R6, OUTPUT);
  pinMode(L7, OUTPUT);
  pinMode(C7, OUTPUT);
  pinMode(R7, OUTPUT);
}

void loop() {
  // put your main code here, to run repeatedly:
//array PWMspeed = [0, 255/2, 255*.75, 255];
//while 1{
//  for (int i =0; i=length(PWMspeed); i++){

    analogWrite(L1, 190);
    analogWrite(L2, 190);
    analogWrite(L3, 190);
    analogWrite(L4, 190);
    analogWrite(L5, 190);
    analogWrite(L6, 190);
    analogWrite(L7, 190);
    analogWrite(R1, 0);
    analogWrite(R2, 0);
    analogWrite(R3, 0);
    analogWrite(R4, 0);
    analogWrite(R5, 0);
    analogWrite(R6, 0);
    analogWrite(R7, 0);
    delay(1000);
    
    analogWrite(C1, 190);
    analogWrite(C2, 190);
    analogWrite(C3, 190);
    analogWrite(C4, 190);
    analogWrite(C5, 190);
    analogWrite(C6, 190);
    analogWrite(C7, 190);
    analogWrite(L1, 0);
    analogWrite(L2, 0);
    analogWrite(L3, 0);
    analogWrite(L4, 0);
    analogWrite(L5, 0);
    analogWrite(L6, 0);
    analogWrite(L7, 0);
    delay(1000);
    
    analogWrite(R1, 190);
    analogWrite(R2, 190);
    analogWrite(R3, 190);
    analogWrite(R4, 190);
    analogWrite(R5, 190);
    analogWrite(R6, 190);
    analogWrite(R7, 190);
    analogWrite(C1, 0);
    analogWrite(C2, 0);
    analogWrite(C3, 0);
    analogWrite(C4, 0);
    analogWrite(C5, 0);
    analogWrite(C6, 0);
    analogWrite(C7, 0);
    delay(1000);
  
//  }
//}

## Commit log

2019-05-14 Add files via upload
    Updates to Teensy firmware to read and print multiple bytes sent from BLE. Added needed adafruit library for arduino compatibility
2019-05-14 Files for main PCB and Peripheral PCB sent for fab
    [Main_PCB_BOM_V1.xlsx, Massage_Pad_Main.brd, Massage_Pad_Main.sch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]
2019-05-19 prints basic characters from app
2019-05-22 removed while loop bug
    [MassagePatterns.h, Winter_Demo.ino]
2019-05-23 added onClick for all buttons, fixed FAB color
    [ActivityCustom.java]
2019-05-30 check Vertical Wave, could try interrupt on RTS
